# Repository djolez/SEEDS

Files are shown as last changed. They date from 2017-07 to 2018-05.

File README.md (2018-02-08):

# SEEDS 
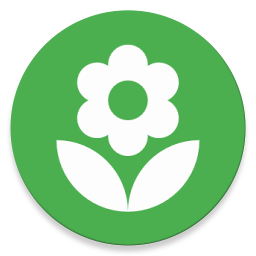
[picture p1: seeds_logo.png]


## Functionalities
The app is based on a _client-server_ approach. First of all, the server interfaces directly to a microcontroller through serial connection, and it represents the entry point to all the devices that can measure the data about the hydroponic system. The board can communicate with connected devices thanks to embedded C scripts that poll the data according to the settings provided by the server. Then, the server runs a web server exposing _REST APIs_ which can be consumed by the client in order to retrieve data. Of course, users can also send data to the server and/or devices through those _APIs_. In fact, a user can set, for the devices that allow it, a range of acceptable values, a time schedule to work in, a polling interval and a check interval and finally which devices to show data about. When setting up the system, the user is able to specify as many boards he preferes, along with the devices attached to it. 

In particular, the data is shown in the client by plotting it in a graph related to a specific device (i.e: data belonging to a specific device, considering all the sub-devices connected to it, are shown in the same graph) with the exception of some kind of devices like relays which can be only toggled.
<br>
In this way, the plant growing can be completely automated in the sense that the only action that the user needs to perform is to change the nutrient solution at the right time.
<br><br><br><br><br>
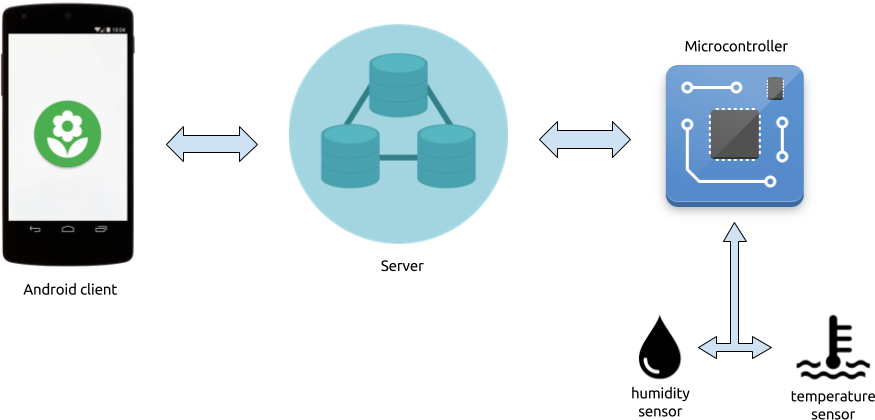
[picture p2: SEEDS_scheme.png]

<br>

## Technologies used
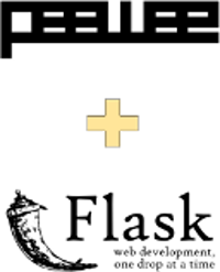
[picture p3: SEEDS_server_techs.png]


The whole system exploits a set of libraries and technologies in order to provide the functionalities mentioned above.
### Server
The server is completely written in python, so it can run even on small embedded systems like RaspberryPi. In particular, it makes use of:
* _Flask_ a micro web framework written in Python used for RESTful request dispatching
* _SQLite_ a lightweight database
* _Peewee_ a simple and small ORM used to easily store data on the underlying SQL database by means of _models_

### Client
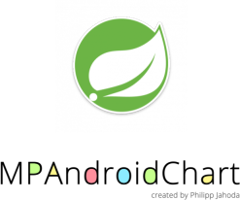
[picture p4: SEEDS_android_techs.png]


The client is represented by an Android application, which uses some opensource libraries to let the user control the server:
* _Spring for Android_ a framework used to provide components of the Spring family like a Rest Client and auth support for accessing secure APIs. It can be found at https://github.com/spring-projects/spring-android
* _Jackson_ a library to serialize a Java Entity to a JSON String and control the mapping process. It can be found at https://github.com/FasterXML/jackson-core
* _PhilJay / MPAndroidChart_ a very easy to use library that cares of taking data and display them in a graph. It supports multiple kind of graphs (in this case, a lineChart), providing high flexibility in terms of retrieving data, operating with them and showing them in a customizable pretty way. It can be found at https://github.com/PhilJay/MPAndroidChart
* _Leavjenn / SmoothDateRangePicker_ an android widget for selecting date range quickly and easily, following Material Design principle.https://github.com/leavjenn/SmoothDateRangePicker

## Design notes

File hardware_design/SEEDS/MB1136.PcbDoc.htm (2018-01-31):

Reporting Options

# File in Previous Format

Date | : | 31-Jan-18
Time | : | 4:49:28 PM
Filename | : | C:\Users\Djordje\workspace\thesis\hardware_design\SEEDS\MB1136.PcbDoc

Version | Warning
Release 12 | CAUTION - Air Gap Width previously controlled by Clearance rule is now controlled by Polygon Connect Style rule's newly introduced Air Gap Width (set to default value). Suggest reviewing each Polygon Connect Style rule's Air Gap Width attribute for correctness.
Release 13 | CAUTION - Silkscreen Over Component Pads Rules are converted to Silk To Solder Mask Clearance Rules. Suggest examining rule scopes for accuracy.

This file was generated by an earlier version of the software

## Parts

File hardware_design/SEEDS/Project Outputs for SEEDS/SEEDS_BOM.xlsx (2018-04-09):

Description | Designator | Footprint | LibRef | Manufacturer | ProductNumber | Quantity | Value | Vendor name | Vendor PN | Price | Stock
 | P2 | dht11 | dht11 |  |  | 1
 | X1 | XTAL_4SM_8X3R8 | MC306 |  |  | 1
Header, 6-Pin, Single row | CN1 | 1*6P | Header 6X1 | Molex | 0022232061 | 1 |  | Digikey | WM4204-ND | 0,41 | 26.758
Capacitor | C8 | 0603C | Cap | AVX Corporation | 06035C102KAT2A | 1 | 1000pF | Digikey | 478-1215-1-ND | 0.10 | 446,246
 | P4 | header_3x2 | header_3x2 | Amphenol FCI | 20021111-00006T4LF | 1 |  | Digikey | 609-3710-ND | 0,45 | 4.920
 | P1 | ds18b20 | ds18b20 | Wurth Electronics | 61300311121 | 1 |  | Digikey | 732-5316-ND | 0,14 | 67.713
Inductor | L1 | INDC1608L | Inductor | Taiyo Yuden | BK1608HS601-T | 1 | 600 OHM | Digikey | 587-1874-1-ND | 0.10 | 40,993
Imported | U6 | RGT16_1P7X1P7 | BQ25504_RGT_16 | Texas Instruments | BQ25504RGTT | 1 |  | Digikey | 296-29741-1-ND | 5,66 | 2.933
Capacitor | CIN | 0603C | Cap | TDK | C1608NP01H472J080AA | 1 | 4700pF | Digikey | 445-14083-1-ND | 0.35 | 9,115
Capacitor (Semiconductor SIM Model) | C3 | 1608[0603] | Cap Semi | AVX Corporation | C1608X5R1H104K080AA | 5 | 0.1µF | Digikey | 478-6206-1-ND | 0.29 | 35
Resistor | ROC2 | 0603R | Res1 | Vishay Dale | CRCW06034M12FKEA | 1 | 4.12M | Digikey | 541-4.12MHCT-ND | 0,10 | 15,060
Resistor | RUV1 | 0603R | Res1 | Vishay Dale | CRCW06034M99FKEA | 2 | 4.99Mohm | Digikey | 541-4.99MHCT-ND | 0.10 | 103,539
Resistor | ROK2 | 0603R | Res1 | Vishay Dale | CRCW06035M23FKEA | 1 | 5.23Mohm | Digikey | 541-5.23MHCT-ND | 0.10 | 18,443
Resistor | ROC1 | 0603R | Res1 | Vishay Dale | CRCW06035M76FKEA | 1 | 5.76M | Digikey | 541-5.76MHCT-ND | 0.10 | 39,086
Resistor | R6 | 0603R | Res1 | Rohm Semiconductor | ESR03EZPJ511 | 1 | 510 Ohms | Digikey | RHM510DCT-ND | 0.10 | 24,289
Capacitor | C1, C2 | 0603C | Cap | Murata Electronics North America | GRM1885C1H100JA01D | 4 | 10pF | Digikey | 490-1403-1-ND | 0,10 | 119.425
Capacitor | C9 | 0603C | Cap | Murata Electronics North America | GRM188R61C225KE15D | 1 | 2.2µF | Digikey | 490-3296-1-ND | 0.14 | 1,593
Capacitor | CSTOR | 0603C | Cap | Taiyo Yuden | JMK107BJ475KA-T | 1 | 4.7µF | Digikey | 587-1785-1-ND | 0,12 | 190.175
Inductor | LBST | INDC1608L | Inductor | Johanson Technology | L-14C22NJV4T | 1 | 22nH | Digikey | 712-1438-1-ND | 0.10 | 25,025
Typical RED, GREEN, YELLOW, AMBER GaAs LED | LD1 | 0603D | LED2 | Lite-On | LTST-C190KGKT | 1 | 571nm | Digikey | 160-1435-1-ND | 0.27 | 1,780,452
 | BT1 | BATTERY | battery | Harwin Inc. | M20-9990246 | 6 |  | Digikey | 952-2262-ND | 0,11 | 39.078
Resistor | ROK3 | 0603R | Res1 | Yageo | RC0603FR-07909KL | 1 | 909 kOhms | Digikey | 311-909KHRCT-ND | 0.10 | 129,610
Resistor | R9 | 0603R | Res1 | Yageo | RC0603JR-070RL | 1 | 0ohm | Digikey | 311-0.0GRCT-ND | 0,10 | 9.866.782
Resistor | ROC1P | 0603R | Res1 | Yageo | RC0603JR-0710ML | 1 | 10M | Digikey | 311-10MGRCT-ND | 0,10 | 580.946
Resistor | R1, R2, R3, R4, R5 | 0603R | Res1 | Yageo | RC0603JR-074K7L | 5 | 4.7 kOhms | Digikey | 311-4.7KGRCT-ND | 0,10 | 3.704.975
 | U1 | XCVR_RFM95W-868S2 | RFM95W-868S2 | RF Solutions | RFM95W-868S2 | 1 |  | Digikey | RFM95W-868S2-ND | 15,16 | 467
Resistor | ROK1 | 0603R | Res1 | Stackpole Electronics Inc. | RMCF0603FT3M74 | 1 | 3.74Mohm | Digikey | RMCF0603FT3M74CT-ND | 0,08 | 1.152
Resistor | ROV1 | 0603R | Res1 | Stackpole Electronics Inc. | RMCF0603FT4M53 | 1 | 4.53Mohm | Digikey | RMCF0603FT4M53CT-ND | 0,08 | 9 501
Resistor | ROV2 | 0603R | Res1 | Stackpole Electronics Inc. | RMCF0603FT5M62 | 1 | 5.62Mohm | Digikey | RMCF0603FT5M62CT-ND | 0,08 | 9.800
Resistor | R7, R8 | 0603R | Res1 | Susumu | RR0816P-102-D | 2 | 1 kOhm | Digikey | RR08P1.0KDCT-ND | 0.11 | 492,396
 | U2 | LQFP64 | MCU_LQFP64 | STM | STM32L476RGT6 | 1 |  | Mouser | 511-STM32L476RGT6 | 7,76 | 4.505
IC REG LINEAR 3V 150MA SOT23-5 | U7 | SOT95P280X110-5N | TPS78330DDCR | Texas Instruments | TPS78330DDCR | 1 |  | Digikey | 296-25880-1-ND | 0,83 | 2.618
Solar cell |  |  | SLMD121H04L | IXYS | SLMD121H04L | 1 |  | Digikey | SLMD121H04L-ND | 4,78 | 965
Female header (2pin) |  |  | PPTC021LFBN-RC | Sullins Connector Solutions | PPTC021LFBN-RC | 3 |  | Digikey | S7000-ND | 0,26000 | 35.95
Female header (3pin) |  |  | PPPC031LFBN-RC | Sullins Connector Solutions | PPPC031LFBN-RC | 1 |  | Digikey | S7036-ND | 0,30000 | 17.876
Enclosure |  |  | 1591XXLBK | Hammond Manufacturing | 1591XXLBK | 1 |  | Digikey | HM1168-ND | 4,36 | 116
Battery |  |  | LP603450 | CELLEVIA BATTERIES | LP244798 | 1 |  | TME | ACCU-LP244798HV/CL | 8.23 | 18

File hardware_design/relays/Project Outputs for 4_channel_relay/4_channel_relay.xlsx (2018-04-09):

Comment | Description | Designator | Footprint | Manufacturer | ProductNumber | Quantity | Price | Stock | Value | Vendor Name | Vendor PN
100nF | Capacitor | C1, C5, C6, C7, C8 | 0603C | AVX Corporation, TDK, TDK, TDK, TDK | C1608X5R1H104K080AA | 7 | 0.29 | 35 | 0.1µF | Digikey | 478-6206-1-ND
10pF[N/A] | Capacitor | C2, C3 | 0603C | Murata Electronics North America | GRM1885C1H100JA01D | 2 | 0,08 | 119.425 | 10pF | Digikey | 490-1403-1-ND
Header 6X1 | Header, 6-Pin, Single row | CN1 | 1*6P | Molex | 0022232061 | 1 | 0.41 | 26,758 |  | Digikey | WM4204-ND
fuse | 240VAC 1A | F1 | fuse | Bel Fuse Inc. | RST 1-BULK | 1 | 0.36 | 11,016 | 1A 250VAC | Digikey | 507-1176-ND
Bead | Inductor | L1 | INDC1608L | Taiyo Yuden | BK1608HS601-T | 1 | 0.10 | 40,993 | 600 OHM | Digikey | 587-1874-1-ND
Green | Typical RED, GREEN, YELLOW, AMBER GaAs LED | LD1 | 0603D | Lite-On | LTST-C190KGKT | 1 | 0,27 | 1.780.452 | 571nm | Digikey | 160-1435-1-ND
MAX4821 |  | M1 | MAX4821 | Maxim Integrated | MAX4821EUP+ | 1 | 2,59 | 2.209 |  | Digikey | MAX4821EUP+-ND
relay_header_3 |  | P1, P2, P3, P4 | ac_header_3 | On Shore Technology | OSTTC032162 | 4 | 0,85 | 17.309 |  | Digikey | ED2610-ND
AC_HEADER |  | P5 | ac_header_2 | On Shore Technology | OSTTC022162 | 1 | 0,80 | 48.711 |  | Digikey | ED2609-ND
50 | Resistor | R1, R2, R3, R4, R9, R10, R11, R12 | 0603R | Vishay Dale | CRCW060350R0FKEA | 8 | 0.0169 | 12,926 | 50 Ohms | Farnell | 2112878
4K7 | Resistor | R5, R6 | 0603R | Yageo | RC0603JR-074K7L | 2 | 0,10 | 3.704.975, [NoValue] | 4.7 kOhms | Digikey | 311-4.7KGRCT-ND
510 | Resistor | R7 | 0603R | Rohm Semiconductor | ESR03EZPJ511 | 1 | 0.10 | 24,289 | 510 Ohms | Digikey | RHM510DCT-ND
 | Resistor | R8 | varistor | Epcos (TDK) | B72205S0231K101 | 1 | 0.40 | 1,230 | 360V 400A | Digikey | 495-6478-ND
ADW1103W |  | REL1, REL2, REL3, REL4 | ADW1103W | Panasonic | ADW1103W | 4 | 6,21 | 85 |  | Mouser | 769-ADW1103TW
MCU_LQFP64 |  | U1 | LQFP64 | STM | STM32L476RGT6 | 1 | 7,76 | 4.505 |  | Mouser | 511-STM32L476RGT6
RAC01-3.3SC | AC/DC converter | U2 | RAC01-3.3SC | Recom Power | RAC01-3.3SC | 1 | 10,63 | 268 |  | Mouser | 919-RAC01-3.3SC
RFM95W-868S2 |  | U3 | XCVR_RFM95W-868S2 | RF Solutions | RFM95W-868S2 | 1 | 15,16 | 467 |  | Digikey | RFM95W-868S2-ND
32.768K[N/A] |  | X1 | XTAL_4SM_8X3R8 |  |  | 1 |  |  |  | Digikey
Jumper |  |  |  | Sullins | QPC02SXGN-RC | 3 | 0,10 | 325.500 |  | Digikey | S9337-ND

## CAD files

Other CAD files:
hardware_design/SEEDS/seeds.DWG
hardware_design/SEEDS/1591LF2SBK.dwg

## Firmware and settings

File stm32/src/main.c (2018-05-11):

/**
 ******************************************************************************
 * @file    main.c
 * @author  Ac6
 * @version V1.0
 * @date    01-December-2013
 * @brief   Default main function.
 ******************************************************************************
 */

/*
 / _____)             _              | |
 ( (____  _____ ____ _| |_ _____  ____| |__
 \____ \| ___ |    (_   _) ___ |/ ___)  _ \
 _____) ) ____| | | || |_| ____( (___| | | |
 (______/|_____)_|_|_| \__)_____)\____)_| |_|
 (C)2013 Semtech

 Description: Ping-Pong implementation

 License: Revised BSD License, see LICENSE.TXT file include in the project

 Maintainer: Miguel Luis and Gregory Cristian
 */
/******************************************************************************
 * @file    main.c
 * @author  MCD Application Team
 * @version V1.1.2
 * @date    08-September-2017
 * @brief   this is the main!
 ******************************************************************************
 * @attention
 *
 * <h2><center>&copy; Copyright (c) 2017 STMicroelectronics International N.V.
 * All rights reserved.</center></h2>
 *
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
 ******************************************************************************
 */

/* Includes ------------------------------------------------------------------*/
#include <string.h>
#include "stm32l4xx_nucleo.h"
#include "stm32l4xx.h"
#include "hw.h"
#include "radio.h"
#include "timeServer.h"
#include "delay.h"
#include "low_power.h"
#include "vcom.h"
#include "lora.h"

#include "config.h"
//#include "communication.h"
#include "manager.h"

extern LPTIM_HandleTypeDef hlptim1;

/*	LORA_CONF	*/

typedef enum {
	LOWPOWER, RX, RX_TIMEOUT, RX_ERROR, TX, TX_TIMEOUT,
} States_t;

#define APP_TX_DUTYCYCLE                            10000
#define LORAWAN_ADR_ON                              0
#define LORAWAN_CONFIRMED_MSG                    DISABLE
#define LORAWAN_APP_PORT                            111
#define LORAWAN_DEFAULT_DATARATE                    DR_5
#define JOINREQ_NBTRIALS                            3

static LoRaParam_t LoRaParamInit = { TX_ON_EVENT,
APP_TX_DUTYCYCLE, CLASS_A,
LORAWAN_ADR_ON, LORAWAN_DEFAULT_DATARATE, LORAWAN_PUBLIC_NETWORK,
JOINREQ_NBTRIALS };

/* call back when LoRa will transmit a frame*/
static void LoraTxData(lora_AppData_t *AppData, FunctionalState* IsTxConfirmed);

/* call back when LoRa has received a frame*/
static void LoraRxData(lora_AppData_t *AppData);

static LoRaMainCallback_t LoRaMainCallbacks = { HW_GetBatteryLevel,
		HW_GetUniqueId, HW_GetRandomSeed, LoraTxData, LoraRxData };

/*	////LORA_CONF	*/

bool lptim1_expired = false;

typedef enum eManagerState
{
	IDLE,
    WRITE,
	UPDATE,
	UPDATE_ALL,
	WRITE_TO_BUFFER,
	WRITE_TO_BUFFER_ALL,
	UPDATE_SEND_ALL
} ManagerState_t;

ManagerState_t current_manager_state;


/**
 * Main application entry point.
 */
extern Port_t* devices;
int main(void) {

	HAL_Init();

	SystemClock_Config();

	DBG_Init();

	HW_Init();
	GPIO_Init();
	MX_TIM2_Init();
	MX_TIM3_Init();
	MX_LPTIM1_Init();

	lora_Init(&LoRaMainCallbacks, &LoRaParamInit);

	while(1){
//		FunctionalTEST();
		lora_fsm();

		current_manager_state = UPDATE_SEND_ALL;
		OnSendEvent();
		DelayMs(500);
		HAL_GPIO_TogglePin(GPIOA, GPIO_PIN_2);
	}

	lora_Init(&LoRaMainCallbacks, &LoRaParamInit);

//	manager_init_all();
//	manager_update_data_all();

//	seconds = period / (clock_speed / prescaler)
//	period = (seconds * clock_speed) / prescaler

	HAL_LPTIM_Counter_Start_IT(&hlptim1, 2560); //10 seconds
//	HAL_LPTIM_Counter_Start_IT(&hlptim1, 1280); //5 seconds
//	HAL_LPTIM_Counter_Start_IT(&hlptim1, 9000);

	while (1) {
		/* run the LoRa class A state machine*/
		lora_fsm();
		DISABLE_IRQ( );

		/* if an interrupt has occurred after DISABLE_IRQ, it is kept pending
		 * and cortex will not enter low power anyway  */

		if (lora_getDeviceState() == DEVICE_STATE_SLEEP) {
			if(lptim1_expired) {
				current_manager_state = UPDATE_SEND_ALL;
				OnSendEvent();
				lptim1_expired = false;
			}

			LowPower_Handler();
		}
		ENABLE_IRQ();
	}
}

void HAL_LPTIM_AutoReloadMatchCallback(LPTIM_HandleTypeDef *hlptim) {
	if(hlptim->Instance==LPTIM1) {
		lptim1_expired = true;
	}
}

static uint8_t tmp[64];
static void LoraTxData(lora_AppData_t *AppData, FunctionalState* IsTxConfirmed) {

//	memcpy(&AppData->Buff[0], &tmp, 64);
//	AppData->BuffSize = 0;
//	AppData->Port = 0;

	memcpy(&AppData->Buff[0], "F", 1);
	AppData->BuffSize = 1;

//	switch(current_manager_state) {
//		case UPDATE_SEND_ALL: {
////			manager_update_data_all();
////			manager_write_to_buffer_all(AppData);
//			current_manager_state = IDLE;
//		}
//	}
	AppData->Port = LORAWAN_APP_PORT;
//	*IsTxConfirmed =  LORAWAN_CONFIRMED_MSG;
}

static void LoraRxData(lora_AppData_t *AppData) {
	int i = 0;
}

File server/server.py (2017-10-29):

from flask import Flask, request, jsonify, abort
import logging
import json

from models.board import Board
from models.device import Device
from models.device_reading import Device_reading
import helper
import global_vars
import global_handler as gh

logger = logging.getLogger(__name__)

app = Flask(__name__)
app.config.update({"DEBUG": True})

def bad_request(code = 400, msg = "An error occured"):
    response = jsonify({"message": msg})
    response.status_code = code
    return response

# BOARD
@app.route('/board')
def get_board_all():
    boards = Board.get_all()
    return jsonify(helper.list_to_dict(boards))

@app.route('/board/<int:id>')
def get_board(id):
    try:
        board = Board.get_by_id(id)
        return jsonify(board.to_dict())
    except Board.DoesNotExist:
        return bad_request(404, "Board not found")

@app.route('/board/<int:id>/device')
def get_devices_by_board_id(id):
    try:
        board = Board.get_by_id(id)
        res = []
        
        if(board):
            for d in board.devices:
                if(d.parent_id is None):
                    d.sub_devices = d.get_sub_devices()
                    res.append(d)

        return jsonify(helper.list_to_dict(res))
    except Board.DoesNotExist:
        return bad_request(404, "Board not found")

# DEVICE
@app.route('/device/<int:id>')
def get_device(id):
    try:
        device = Device.get_by_id(id)
        return jsonify(device.to_dict())
    except Device.DoesNotExist:
        return bad_request(404, "Device not found")

# DEVICE_READING
@app.route('/device/<int:id>/reading')
def get_all_device_readings(id):
    try:
        device = Device.get_by_id(id)
        return jsonify(helper.list_to_dict(device.readings))
    except Device.DoesNotExist:
        return bad_request(404, "Device not found")

def get_full_device_with_readings(id, start, end):
    try:
        device = Device.get_with_readings(id, start, end)

        return device
    except Device.DoesNotExist:
        return bad_request(404, "Device not found")

@app.route('/device/<int:id>/from/<start_datetime>/to/<end_datetime>')
def get_device_with_readings(id, start_datetime, end_datetime):
    try:
        logger.debug("Fetching device readings id: {}, start: {}, end: {}".format(id, start_datetime, end_datetime))
        start = helper.string_to_datetime(start_datetime)
        end = helper.string_to_datetime(end_datetime)
        res = get_full_device_with_readings(id, start, end)        

        return jsonify(res.to_dict())
    except Device.DoesNotExist:
        return bad_request(404, "Device not found")
    except Exception as e:
        logger.exception(e)
        return bad_request()

@app.route('/device/from/<start_datetime>/to/<end_datetime>', methods = ["POST"])
def get_readings_from_devices_list(start_datetime, end_datetime):
    ids = request.form.getlist('ids')
    print(ids)
    start = helper.string_to_datetime(start_datetime)
    end = helper.string_to_datetime(end_datetime)

    res = []
    for id in ids:
        dr = get_full_device_with_readings(int(id), start, end)
        if(dr is not None):
            res.append(dr.to_dict())
    return jsonify(res)

@app.route('/device/<int:id>/last-reading')
def get_device_last_reading(id):
    try:
        logger.debug("Fetching device last reading, id: {}".format(id))
        device = Device.get_last_reading(id)        
        return jsonify(device.to_dict())

    except Device.DoesNotExist:
        return bad_request(404, "Device not found")
    except Exception as e:
        logger.exception(e)
        return bad_request()

@app.route('/device/<int:id>/write/<int:value>')
def device_write_value(id, value):
    try:
        logger.debug("Writing to a device, id: {}, value: {}".format(id, value))
        device = Device.get_by_id(id)
        device.write(value)

        return ("OK")

    except Device.DoesNotExist:
        return bad_request(404, "Device not found")
    except Exception as e:
        logger.exception(e)
        return bad_request()


# SETTINGS
@app.route('/settings')
def get_settings():
    return jsonify(global_vars.SETTINGS)

@app.route('/settings', methods = ["POST"])
def save_settings():
    try:
        data = request.get_json(force = True)
        logger.debug(data)
        
        global_vars.SETTINGS = data

        gh.save_settings_to_file()
        
        return("OK")
    except Exception:
        logger.exception("Failed to write settings to a file")
        return bad_request(400, "An error occured while trying to write settings to a file")


def run():
    app.run(host='0.0.0.0', use_reloader=False)

if __name__ == '__main__':
    run()

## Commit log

2017-06-15 Added stm32 directory
2017-06-26 Added read, read_all to the board, added scheduler functionality
2017-06-26 Added API for board, device and device_reading
2017-06-27 Changed device_reading range API
2017-07-03 Working on retrieving device readings API
2017-07-07 Changed sub_devices to be part of the device table, finished cmd_app update_interval functionality, finished get_avg for device
2017-07-09 Rewrite board_init and sync msg parser
2017-07-09 Changed device API to work with new sub_device solution
2017-07-12 API for updating settings, stop active threads on program end
2017-07-13 Finished device get_last_reading, added API
2017-07-13 Tweaking, added error message method to communication module
    [communication.c, manager.c]
2017-07-15 Changed device_reading add method to convert int values to float
2017-07-15 Support for device running times
2017-07-21 Fixed problems with reading cmd
    [communication.c, main.c, manager.c]
2017-07-21 Added debounce to Port interrupt
2017-07-22 Include dates selected by the user to the device search
2017-07-22 Working on device selection dialog
2017-07-25 Changed serial cmd format for device_reading, added error cmd and interrupt (without implementation)
    [config.py, global_handler.py, main.py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]
2017-07-25 Changed serial cmd format for device_reading
2017-07-25 Started working on analog port type, minor bug fixing
    [communication.c, manager.c]
2017-09-08 Introduced selection of Devices
2017-09-09 Introduced different settings layout for relays
2017-09-09 Checkboxes on settings activity are now working
    Added coherency between selected devices and checked checkboxes in
    settings activity.
2017-09-10 Added write API for device
2017-09-16 Added switch and relay to init_db script
2017-09-17 Changed settings view for Relays and Switches
    In settings, schedules and value ranges are not displayed for relays and
    switches devices. Preparing to add logic for this kind of devices.
2017-09-19 Preparing to implement relay switching on/off
2017-09-20 Added AsyncTask to send relay value.
    Added the functionality to set the relay value. This can be done by
    pressing a button showing the relay name in the main screen. The button
    should be presented as pressed if the value of the relay is 1 (set) or
    as normal if the value is 0 (not set). This is to be fixed still!!
2017-09-20 Fixed inserting of doubled relay buttons
2017-09-20 Added row for all sensors in settings activity
    Now all the devices are shown in settings activity list. This means that
    we have settings also for devices (sensors) like humidity and
    temperature.
2017-09-20 Fixed schedule showing in settings
    Schedule settings are now shown only for relay devices. For all other
    types of devices,except switches, only value ranges are shown and editable.
2017-10-05 Fixed bug
    fixed bug in SettingsActivity. Now the dialog doesn't remember fields of
    the last clicked device's settings.
2017-10-13 Fixed bug on showing selected devices
2017-10-23 Fixed various small bugs on server and microcontroller
    [comm_implementation.py, config.py, global_handler.py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]
2017-10-23 Commited missing microcontroller files
    [communication.c, dht11.c, ds18b20.c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]
2017-10-26 Working on bug fixing on server and microcontroller part
    [config.py, global_handler.py]
2017-10-29 Fixed bugs before the presentation
    [config.py, global_handler.py, server.py]
2018-01-11 Added hardware design files to the project
    [1591LF2SBK.dwg, Alarm.PcbLib, Alarm.SchLib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]
2018-01-18 Added solar charger design, minor changes to other parts
    [SEEDS.PrjPcb, TOP.SchDoc, relays.PcbDoc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]
2018-01-19 Polishing sensors board
    [relays.PcbDoc, seeds.PcbDoc, sensors.SchDoc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]
2018-01-22 Fixed minor problems, added CAD model of the enclosure and board cut-out, added silkscreen desc of pins, added voltage regulator to solar charger output
    [SEEDS.PrjPcb, TOP.SchDoc, seeds.PcbDoc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]
2018-01-23 Started changing the relay circuit (first design was bad)
    [relays.SchDoc, seeds.PcbDoc]
2018-01-24 Changed relay circuit to new one
    [MCU.SchDoc, SEEDS.PrjPcb, TOP.SchDoc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]
2018-01-25 Various minor changes
    [4_channel_relay.PcbDoc, 4_channel_relay.PrjPcb, MCU.SchDoc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]
2018-01-29 Changed relay model, fixed track widths
    [4_channel_relay.PcbDoc, 4_channel_relay.PrjPcb, relays.SchDoc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]
2018-01-30 Finished editing power lines, added capacitor to VDD for MAX4821, changed AC header, resized via sizes, added fuse to relay circuit
    [4_channel_relay.PcbDoc, MCU.SchDoc, relays.SchDoc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]
2018-01-31 no time
    [4_channel_relay.PcbDoc, SEEDS.PrjPcb, relays.SchDoc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]
2018-02-01 Changed relay board layout, rewired tracks
    [4_channel_relay.PcbDoc, seeds.PcbDoc, solar.SchDoc]
2018-02-05 working on moving ac converter
    [4_channel_relay.PcbDoc, seeds.PcbDoc, sensors.SchDoc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]
2018-02-06 finished all the tasks, ready for review
    [4_channel_relay.PcbDoc, 4_channel_relay.PrjPcb, SEEDS.PrjPcb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]
2018-02-07 minor changes
    [4_channel_relay.PcbDoc, MCU.SchDoc, seeds.PcbDoc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]
2018-02-08 Working on adding product numbers to all parts
    [4_channel_relay.PcbDoc, MCU.SchDoc, relays.SchDoc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]
2018-02-11 Finished adding part numbers
    [MCU.SchDoc, SEEDS.PrjPcb, seeds.PcbDoc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]
2018-03-13 Safety commit
    [4_channel_relay.GBL, 4_channel_relay.GBO, 4_channel_relay.GBS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]
2018-03-25 Updated BOM and gerber files for both projects
    [4_channel_relay.GBL, 4_channel_relay.GBO, 4_channel_relay.GBS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]
2018-04-09 Fixed all DRC errors
    [4_channel_relay.PcbDoc, 4_channel_relay.PrjPcb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]
2018-04-11 Updated rules to match EuroCircuit, fixed resulting errors
    [4_channel_relay.PcbDoc, seeds.PcbDoc, solar.SchDoc]
2018-04-13 Commit all
    [4_channel_relay.PcbDoc, 4_channel_relay.PrjPcb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]
2018-05-09 Resolved merge conflict with lora_low_power
    [Test.c, communication.c, debug.c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]
